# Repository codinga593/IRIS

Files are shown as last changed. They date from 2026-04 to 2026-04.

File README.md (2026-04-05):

# IRIS
IRIS Is a high powered model rocket focused on a precise propulsive landing on a custom tower, similar to SpaceX's falcon 9. It will fly on a H45 motor to approximately 700m, guiding itself to a waypoint in the air using aerodynamic fin control. It will then begin a controlled descent where fins attempt to maintain x and y pos. A landing motor (F15) then ignites to kill velocity, as thrust vectoring helps guide it to the tower where it will be caught by two motorised arms.

This project, while ambitous will be split into serveral mid power and high power flights to test subsystems and more. At the heart of the rocket is the amethyst flight computer, along with two extra boards- a compute module 5 and a raspberry pi zero 2 w. The compute module five will run non linear model predicitive control, an insanely powerful control algorithm to determine required X and Y accels to reach the target given fin or tvc limits. The STM32 based flight computer then turns these accelerations into concrete actuator commands. AN ADDED layer of abstraction is present for the fins in the form of field oriented control, which maintains torque to prevent backdriving.

Screenshot 2026-04-05 at 4 58 04 pm

Pictured above: FULL CAD of IRIS with transparent airframe for visibility

Screenshot 2026-03-22 at 3 32 23 pm

Pictured above: AMETHYST rocket flight computer. Note: Silkscreen colour is subject to change.

Screenshot 2026-03-17 at 5 57 23 pm

Pictured Above: Final Avionics Bay design on IRIS

# Bill of Materials (BOM)

| Designator | Part Name | Qty | Value / Part Number | Link |
|---|---:|---:|---|---|
| C66,C95,C26,C49,C28,C67,C55,C29,C33,C22,C48,C54,C19,C34,C30,C58,C41,C42,C20,C45,C46,C39,C18,C93,C47,C32,C21,C25,C27,C88,C35 | Ceramic Capacitor | 31 | 100nF, 0402, Samsung CL05B104KO5NNNC (JLC C1525) | [Link](https://jlcpcb.com/partdetail/1877-CL05B104KO5NNNC/C1525) |
| C23,C24,C61,C60 | Ceramic Capacitor | 4 | 24pF, 0402, C0G/NP0, FH 0402CG240J500NT (LCSC C1553) | [Link](https://www.lcsc.com/product-detail/C1553.html) |
| U3 | IMU | 1 | BNO085 (JLC C5189642) | [Link](https://jlcpcb.com/partdetail/CEVA-BNO085/C5189642) |
| J9,J1,J10,J11 | Socket Header | 4 | 1x03, 2.54mm, vertical, Amphenol SIP050-1X03-157BLF | [Link](https://www.digikey.com/en/products/detail/amphenol-cs-fci/SIP050-1X03-157BLF/1541044) |
| R45,R48,R46,R47,R49,R44 | Resistor | 6 | TBD - source BOM only says 'R' (exact value not specified) |  |
| R21,R14,R22,R17 | Resistor | 4 | 4.7kΩ, 0603, UNI-ROYAL 0603WAF4701T5E (LCSC C23162) | [Link](https://www.lcsc.com/product-detail/C23162.html) |
| TP13,TP9,TP14,TP6,TP11,TP10,TP16,TP15,TP5,TP8,TP7 | Test Point | 11 | PCB test pad 1.0x1.0mm - no discrete purchasable part specified |  |
| URpiZero1,UCM4 | Socket Header | 2 | 2x20 Raspberry Pi socket/riser header, Adafruit 4079 | [Link](https://www.digikey.com.au/en/products/detail/adafruit-industries-llc/4079/9858462) |
| R10,R18,R28 | Resistor | 3 | 100kΩ, 0402, UNI-ROYAL 0402WGF1003TCE (JLC/LCSC C25741) | [Link](https://www.lcsc.com/product-detail/C25741.html) |
| Q2,Q4,Q3 | MOSFET | 3 | BSZ100N06LS3 G, Infineon | [Link](https://www.digikey.com/en/products/detail/infineon-technologies/BSZ100N06LS3GATMA1/1936392) |
| C53,C92,C90,C94 | Ceramic Capacitor | 4 | 10uF, 0402, Samsung CL05A106MQ5NUNC (JLC C15525) | [Link](https://jlcpcb.com/partdetail/16204-CL05A106MQ5NUNC/C15525) |
| R6,R32,R8,R1 | Resistor | 4 | 100Ω, 0402, Ever Ohms CR0402F100RQ10 (JLC C429511) | [Link](https://jlcpcb.com/partdetail/Ever_OhmsTech-CR0402F100RQ10/C429511) |
| J14 | Pin Header | 1 | 1x04, 2.54mm, vertical, generic 4-pin header | [Link](https://newhavendisplay.com/1x4-single-row-pin-header-connector/) |
| J17 | RF Connector | 1 | Hirose U.FL-R-SMT(01) | [Link](https://www.digikey.com.au/en/products/detail/hirose-electric-co-ltd/U-FL-R-SMT-01/513010) |
| U5 | Barometer | 1 | MS5611-01BA03 / MS561101BA03-50 (JLC C15639) | [Link](https://jlcpcb.com/partdetail/TEConnectivity-MS561101BA0350/C15639) |
| C37 | Ceramic Capacitor | 1 | 10uF, 0603, Samsung CL10A106MA8NRNC (LCSC C96446) | [Link](https://www.lcsc.com/product-detail/C96446.html) |
| C91,C86,C89 | Ceramic Capacitor | 3 | 22uF, 0402, JLCPCB Assembly 22uF/16V (JLC C9900105298) | [Link](https://jlcpcb.com/partdetail/JLCPCBAssembly-22uF16V/C9900105298) |
| C84,C85 | Ceramic Capacitor | 2 | 10pF, 0402, FH 0402CG100J500NT (JLC C1545) | [Link](https://jlcpcb.com/partdetail/1897-0402CG100J500NT/C1545) |
| L11,L10,L9 | Inductor | 3 | 6.8uH, Würth WE-XHMA 6060 | [Link](https://www.mouser.com/ProductDetail/Wurth-Elektronik/74437368068) |
| R34,R33 | Resistor | 2 | 22Ω, 0402, YAGEO RC0402FR-0722RL (LCSC C114765) | [Link](https://www.lcsc.com/product-detail/C114765.html) |
| J5,J3,J4 | Terminal Block | 3 | Same Sky / CUI TB002-500-02BE | [Link](https://www.digikey.com.au/en/products/detail/same-sky-formerly-cui-devices/TB002-500-02BE/10064069) |
| Y1,Y3 | Crystal | 2 | 24MHz, 3225, Suzhou Liming 3225-24.00-20-10-10/A (JLC C518165) | [Link](https://jlcpcb.com/partdetail/534702-3225_24_00_20_10_10A/C518165) |
| C31 | Ceramic Capacitor | 1 | 10uF, 0402, Samsung CL05A106MQ5NUNC (JLC C15525) | [Link](https://jlcpcb.com/partdetail/16204-CL05A106MQ5NUNC/C15525) |
| J6 | JST Header | 1 | JST B5B-XH-A, 5-pin, 2.50mm, vertical | [Link](https://www.digikey.com/en/products/detail/jst-sales-america-inc/B5B-XH-A/1530483) |
| IC2 | LoRa Module | 1 | Seeed 114993390 / Wio-SX1262 | [Link](https://www.digikey.com/en/products/detail/seeed-technology-co-ltd/114993390/25835823) |
| U2 | LDO Regulator | 1 | AMS1117-3.3, SOT-223 (JLC C6186) | [Link](https://jlcpcb.com/partdetail/Advanced_MonolithicSystems-AMS1117_33/C6186) |
| U4 | IMU | 1 | ICM-42688-P (JLC C1850418) | [Link](https://jlcpcb.com/partdetail/TDKInvenSense-ICM_42688P/C1850418) |
| U11,U12,U13 | Buck Converter | 3 | TPS54525PWPR (JLC C140350) | [Link](https://jlcpcb.com/partdetail/TexasInstruments-TPS54525PWPR/C140350) |
| C36,C38,C56 | Ceramic Capacitor | 3 | 100nF, 0603, YAGEO CC0603KRX7R9BB104 (LCSC C14663) | [Link](https://www.lcsc.com/product-detail/C14663.html) |
| IC1 | NOR Flash | 1 | W25Q128JVFIQ (JLC C111478) | [Link](https://jlcpcb.com/partdetail/WinbondElec-W25Q128JVFIQ/C111478) |
| R15,R2,R7,R9,R11,R5,R29,R12,R27 | Resistor | 9 | 10kΩ, 0402, UNI-ROYAL 0402WGF1002TCE (JLC C25744) | [Link](https://jlcpcb.com/partdetail/26487-0402WGF1002TCE/C25744) |
| R3,R4 | Resistor | 2 | 1.5kΩ, 0402, UNI-ROYAL 0402WGF1501TCE (LCSC C25867) | [Link](https://www.lcsc.com/product-detail/C25867.html) |
| U1 | MCU | 1 | STM32H753ZIT6 (JLC C730207) | [Link](https://jlcpcb.com/partdetail/STMicroelectronics-STM32H753ZIT6/C730207) |
| C3,C2 | Ceramic Capacitor | 2 | 22uF, 0805, Samsung CL21A226MAYNNNE (LCSC C45783) | [Link](https://www.lcsc.com/product-detail/C45783.html) |
| C59 | Ceramic Capacitor | 1 | 10nF, 0402, Kyocera AVX 0402YC103K4T2A (JLC C2172121) | [Link](https://jlcpcb.com/partdetail/KyoceraAVX-0402YC103K4T2A/C2172121) |
| Y4 | Crystal | 1 | TBD - source BOM says only 'Crystal' in 2012 package |  |
| IC7 | Radar Sensor | 1 | Acconeer A121-001-T&R / A121 | [Link](https://www.mouser.com/ProductDetail/Acconeer/A121-001-TR) |
| D2 | LED | 1 | TBD - source BOM says only 'LED' in 0402 package |  |
| C1 | Ceramic Capacitor | 1 | 10uF, 0402, Samsung CL05A106MQ5NUNC (JLC C15525) | [Link](https://jlcpcb.com/partdetail/16204-CL05A106MQ5NUNC/C15525) |
| J7 | Molex PicoBlade Header | 1 | Molex 53261-0471 | [Link](https://www.digikey.com/en/products/detail/molex/0532610471/699096) |
| C40,C17 | Ceramic Capacitor | 2 | 2.2uF, 0402, Samsung CL05A225MQ5NSNC (JLC C12530) | [Link](https://jlcpcb.com/partdetail/13164-CL05A225MQ5NSNC/C12530) |
| J18 | USB Connector | 1 | Würth 629105150521, Micro USB B | [Link](https://www.digikey.com.au/en/products/detail/w%C3%BCrth-elektronik/629105150521/5047751) |
| U7 | Level Shifter | 1 | TXS0108EPWR (JLC C17206) | [Link](https://jlcpcb.com/partdetail/TexasInstruments-TXS0108EPWR/C17206) |
| FB1 | Ferrite Bead | 1 | Sunlord GZ1608D601TF (JLC C1002) | [Link](https://jlcpcb.com/partdetail/Sunlord-GZ1608D601TF/C1002) |
| D3 | Schottky Diode | 1 | BAT54A, SOT-23 (JLC C397609) | [Link](https://jlcpcb.com/partdetail/AnBon-BAT54A/C397609) |
| J12 | JST Header | 1 | JST S2B-XH-A, 2-pin, 2.50mm, right-angle | [Link](https://www.digikey.com/en/products/detail/jst-sales-america-inc/S2B-XH-A/1651055) |
| U10 | GNSS Module | 1 | u-blox MAX-M10S-00B (JLC C4153167) | [Link](https://jlcpcb.com/partdetail/UBLOX-MAX_M10S00B/C4153167) |
| J8 | XT30 Connector | 1 | AMASS XT30U-M (JLC C99101) | [Link](https://jlcpcb.com/partdetail/Changzhou_AmassElec-XT30UM/C99101) |
| R20,R19 | Resistor | 2 | 10kΩ, 0603, YAGEO RC0603FR-0710KL (LCSC C98220) | [Link](https://www.lcsc.com/product-detail/C98220.html) |
| J2 | JST Header | 1 | JST B2B-XH-A, 2-pin, 2.50mm, vertical | [Link](https://www.digikey.com/en/products/detail/jst-sales-america-inc/B2B-XH-A/1651045) |

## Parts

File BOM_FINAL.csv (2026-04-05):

Designator | Part Name | Qty | Value / Part Number | Link
C66,C95,C26,C49,C28,C67,C55,C29,C33,C22,C48,C54,C19,C34,C30,C58,C41,C42,C20,C45,C46,C39,C18,C93,C47,C32,C21,C25,C27,C88,C35 | Ceramic Capacitor | 31 | 100nF, 0402, Samsung CL05B104KO5NNNC (JLC C1525) | https://jlcpcb.com/partdetail/1877-CL05B104KO5NNNC/C1525
C23,C24,C61,C60 | Ceramic Capacitor | 4 | 24pF, 0402, C0G/NP0, FH 0402CG240J500NT (LCSC C1553) | https://www.lcsc.com/product-detail/C1553.html
U3 | IMU | 1 | BNO085 (JLC C5189642) | https://jlcpcb.com/partdetail/CEVA-BNO085/C5189642
J9,J1,J10,J11 | Socket Header | 4 | 1x03, 2.54mm, vertical, Amphenol SIP050-1X03-157BLF | https://www.digikey.com/en/products/detail/amphenol-cs-fci/SIP050-1X03-157BLF/1541044
R45,R48,R46,R47,R49,R44 | Resistor | 6 | TBD - source BOM only says 'R' (exact value not specified)
R21,R14,R22,R17 | Resistor | 4 | 4.7kΩ, 0603, UNI-ROYAL 0603WAF4701T5E (LCSC C23162) | https://www.lcsc.com/product-detail/C23162.html
TP13,TP9,TP14,TP6,TP11,TP10,TP16,TP15,TP5,TP8,TP7 | Test Point | 11 | PCB test pad 1.0x1.0mm - no discrete purchasable part specified
URpiZero1,UCM4 | Socket Header | 2 | 2x20 Raspberry Pi socket/riser header, Adafruit 4079 | https://www.digikey.com.au/en/products/detail/adafruit-industries-llc/4079/9858462
R10,R18,R28 | Resistor | 3 | 100kΩ, 0402, UNI-ROYAL 0402WGF1003TCE (JLC/LCSC C25741) | https://www.lcsc.com/product-detail/C25741.html
Q2,Q4,Q3 | MOSFET | 3 | BSZ100N06LS3 G, Infineon | https://www.digikey.com/en/products/detail/infineon-technologies/BSZ100N06LS3GATMA1/1936392
C53,C92,C90,C94 | Ceramic Capacitor | 4 | 10uF, 0402, Samsung CL05A106MQ5NUNC (JLC C15525) | https://jlcpcb.com/partdetail/16204-CL05A106MQ5NUNC/C15525
R6,R32,R8,R1 | Resistor | 4 | 100Ω, 0402, Ever Ohms CR0402F100RQ10 (JLC C429511) | https://jlcpcb.com/partdetail/Ever_OhmsTech-CR0402F100RQ10/C429511
J14 | Pin Header | 1 | 1x04, 2.54mm, vertical, generic 4-pin header | https://newhavendisplay.com/1x4-single-row-pin-header-connector/
J17 | RF Connector | 1 | Hirose U.FL-R-SMT(01) | https://www.digikey.com.au/en/products/detail/hirose-electric-co-ltd/U-FL-R-SMT-01/513010
U5 | Barometer | 1 | MS5611-01BA03 / MS561101BA03-50 (JLC C15639) | https://jlcpcb.com/partdetail/TEConnectivity-MS561101BA0350/C15639
C37 | Ceramic Capacitor | 1 | 10uF, 0603, Samsung CL10A106MA8NRNC (LCSC C96446) | https://www.lcsc.com/product-detail/C96446.html
C91,C86,C89 | Ceramic Capacitor | 3 | 22uF, 0402, JLCPCB Assembly 22uF/16V (JLC C9900105298) | https://jlcpcb.com/partdetail/JLCPCBAssembly-22uF16V/C9900105298
C84,C85 | Ceramic Capacitor | 2 | 10pF, 0402, FH 0402CG100J500NT (JLC C1545) | https://jlcpcb.com/partdetail/1897-0402CG100J500NT/C1545
L11,L10,L9 | Inductor | 3 | 6.8uH, Würth WE-XHMA 6060 | https://www.mouser.com/ProductDetail/Wurth-Elektronik/74437368068
R34,R33 | Resistor | 2 | 22Ω, 0402, YAGEO RC0402FR-0722RL (LCSC C114765) | https://www.lcsc.com/product-detail/C114765.html
J5,J3,J4 | Terminal Block | 3 | Same Sky / CUI TB002-500-02BE | https://www.digikey.com.au/en/products/detail/same-sky-formerly-cui-devices/TB002-500-02BE/10064069
Y1,Y3 | Crystal | 2 | 24MHz, 3225, Suzhou Liming 3225-24.00-20-10-10/A (JLC C518165) | https://jlcpcb.com/partdetail/534702-3225_24_00_20_10_10A/C518165
C31 | Ceramic Capacitor | 1 | 10uF, 0402, Samsung CL05A106MQ5NUNC (JLC C15525) | https://jlcpcb.com/partdetail/16204-CL05A106MQ5NUNC/C15525
J6 | JST Header | 1 | JST B5B-XH-A, 5-pin, 2.50mm, vertical | https://www.digikey.com/en/products/detail/jst-sales-america-inc/B5B-XH-A/1530483
IC2 | LoRa Module | 1 | Seeed 114993390 / Wio-SX1262 | https://www.digikey.com/en/products/detail/seeed-technology-co-ltd/114993390/25835823
U2 | LDO Regulator | 1 | AMS1117-3.3, SOT-223 (JLC C6186) | https://jlcpcb.com/partdetail/Advanced_MonolithicSystems-AMS1117_33/C6186
U4 | IMU | 1 | ICM-42688-P (JLC C1850418) | https://jlcpcb.com/partdetail/TDKInvenSense-ICM_42688P/C1850418
U11,U12,U13 | Buck Converter | 3 | TPS54525PWPR (JLC C140350) | https://jlcpcb.com/partdetail/TexasInstruments-TPS54525PWPR/C140350
C36,C38,C56 | Ceramic Capacitor | 3 | 100nF, 0603, YAGEO CC0603KRX7R9BB104 (LCSC C14663) | https://www.lcsc.com/product-detail/C14663.html
IC1 | NOR Flash | 1 | W25Q128JVFIQ (JLC C111478) | https://jlcpcb.com/partdetail/WinbondElec-W25Q128JVFIQ/C111478
R15,R2,R7,R9,R11,R5,R29,R12,R27 | Resistor | 9 | 10kΩ, 0402, UNI-ROYAL 0402WGF1002TCE (JLC C25744) | https://jlcpcb.com/partdetail/26487-0402WGF1002TCE/C25744
R3,R4 | Resistor | 2 | 1.5kΩ, 0402, UNI-ROYAL 0402WGF1501TCE (LCSC C25867) | https://www.lcsc.com/product-detail/C25867.html
U1 | MCU | 1 | STM32H753ZIT6 (JLC C730207) | https://jlcpcb.com/partdetail/STMicroelectronics-STM32H753ZIT6/C730207
C3,C2 | Ceramic Capacitor | 2 | 22uF, 0805, Samsung CL21A226MAYNNNE (LCSC C45783) | https://www.lcsc.com/product-detail/C45783.html
C59 | Ceramic Capacitor | 1 | 10nF, 0402, Kyocera AVX 0402YC103K4T2A (JLC C2172121) | https://jlcpcb.com/partdetail/KyoceraAVX-0402YC103K4T2A/C2172121
Y4 | Crystal | 1 | TBD - source BOM says only 'Crystal' in 2012 package
IC7 | Radar Sensor | 1 | Acconeer A121-001-T&R / A121 | https://www.mouser.com/ProductDetail/Acconeer/A121-001-TR
D2 | LED | 1 | TBD - source BOM says only 'LED' in 0402 package
C1 | Ceramic Capacitor | 1 | 10uF, 0402, Samsung CL05A106MQ5NUNC (JLC C15525) | https://jlcpcb.com/partdetail/16204-CL05A106MQ5NUNC/C15525
J7 | Molex PicoBlade Header | 1 | Molex 53261-0471 | https://www.digikey.com/en/products/detail/molex/0532610471/699096
C40,C17 | Ceramic Capacitor | 2 | 2.2uF, 0402, Samsung CL05A225MQ5NSNC (JLC C12530) | https://jlcpcb.com/partdetail/13164-CL05A225MQ5NSNC/C12530
J18 | USB Connector | 1 | Würth 629105150521, Micro USB B | https://www.digikey.com.au/en/products/detail/w%C3%BCrth-elektronik/629105150521/5047751
U7 | Level Shifter | 1 | TXS0108EPWR (JLC C17206) | https://jlcpcb.com/partdetail/TexasInstruments-TXS0108EPWR/C17206
FB1 | Ferrite Bead | 1 | Sunlord GZ1608D601TF (JLC C1002) | https://jlcpcb.com/partdetail/Sunlord-GZ1608D601TF/C1002
D3 | Schottky Diode | 1 | BAT54A, SOT-23 (JLC C397609) | https://jlcpcb.com/partdetail/AnBon-BAT54A/C397609
J12 | JST Header | 1 | JST S2B-XH-A, 2-pin, 2.50mm, right-angle | https://www.digikey.com/en/products/detail/jst-sales-america-inc/S2B-XH-A/1651055
U10 | GNSS Module | 1 | u-blox MAX-M10S-00B (JLC C4153167) | https://jlcpcb.com/partdetail/UBLOX-MAX_M10S00B/C4153167
J8 | XT30 Connector | 1 | AMASS XT30U-M (JLC C99101) | https://jlcpcb.com/partdetail/Changzhou_AmassElec-XT30UM/C99101
R20,R19 | Resistor | 2 | 10kΩ, 0603, YAGEO RC0603FR-0710KL (LCSC C98220) | https://www.lcsc.com/product-detail/C98220.html
J2 | JST Header | 1 | JST B2B-XH-A, 2-pin, 2.50mm, vertical | https://www.digikey.com/en/products/detail/jst-sales-america-inc/B2B-XH-A/1651045

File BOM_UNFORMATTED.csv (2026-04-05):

Id | Designator | Footprint | Quantity | Designation | Supplier and ref
1 | C66,C95,C26,C49,C28,C67,C55,C29,C33,C22,C48,C54,C19,C34,C30,C58,C41,C42,C20,C45,C46,C39,C18,C93,C47,C32,C21,C25,C27,C88,C35 | C_0402_1005Metric | 31 | 100n
2 | C23,C24,C61,C60 | C_0402_1005Metric | 4 | 24pf
3 | U3 | IC_BNO085 | 1 | BNO085
4 | J9,J1,J10,J11 | PinHeader_1x03_P2.54mm_Vertical | 4 | Conn_01x03_Socket
5 | R45,R48,R46,R47,R49,R44 | R_0402_1005Metric | 6 | R
6 | R21,R14,R22,R17 | R_0603_1608Metric | 4 | 4.7k
7 | TP13,TP9,TP14,TP6,TP11,TP10,TP16,TP15,TP5,TP8,TP12 | TestPoint_Pad_1.0x1.0mm | 11 | TestPoint
8 | URpiZero1,UCM4 | PinSocket_2x20_P2.54mm_Vertical_SMD | 2 | ~
9 | R10,R18,R28 | R_0402_1005Metric | 3 | 100k
10 | Q2,Q4,Q3 | TRANS_BSZ100N06LS3_G | 3 | BSZ100N06LS3_G
11 | C53,C92,C90,C94 | C_0402_1005Metric | 4 | 10u
12 | R6,R32,R8,R1 | R_0402_1005Metric | 4 | 100Ω
13 | J14 | PinHeader_1x04_P2.54mm_Vertical | 1 | Conn_01x04
14 | J17 | HRS_U.FL-R-SMT_01_ | 1 | U.FL-R-SMT_01_
15 | U5 | LGA-8_3x5mm_P1.25mm | 1 | MS5611-01BA
16 | C37 | C_0603_1608Metric | 1 | 10u
17 | C91,C86,C89 | C_0402_1005Metric | 3 | 22u
18 | C84,C85 | C_0402_1005Metric | 2 | 10pf
19 | L11,L10,L9 | WE-XHMA_6060 | 3 | 6.8 µH
20 | R34,R33 | R_0402_1005Metric | 2 | 22
21 | J5,J3,J4 | CUI_TB002-500-02BE | 3 | Conn_01x02
22 | Y1,Y3 | TSX-3225 | 2 | 24mhz
23 | C31 | C_0402_1005Metric | 1 | 10uf
24 | J6 | JST_XH_B5B-XH-A_1x05_P2.50mm_Vertical | 1 | Conn_01x05_Pin
25 | IC2 | 114993390 | 1 | 114993390
26 | U2 | SOT-223-3_TabPin2 | 1 | AMS1117-3.3
27 | U4 | PQFN50P300X250X97-14N | 1 | ICM-42688-P
28 | U11,U12,U13 | PWP14_2P31X2P46_TEX | 3 | TPS54525PWPR
29 | C36,C38,C56 | C_0603_1608Metric | 3 | 100n
30 | IC1 | SOIC127P1032X264-16N | 1 | W25Q128JVFIQ
31 | R15,R2,R7,R9,R11,R5,R29,R12,R27 | R_0402_1005Metric | 9 | 10k
32 | R3,R4 | R_0402_1005Metric | 2 | 1k5
33 | U1 | QFP50P2200X2200X160-144N | 1 | STM32H753ZIT6
34 | C3,C2 | C_0805_2012Metric | 2 | 22u
35 | C59 | C_0402_1005Metric | 1 | 10n
36 | Y4 | Crystal_SMD_2012-2Pin_2.0x1.2mm | 1 | Crystal
37 | IC7 | A121001TR | 1 | A121-001-T&R
38 | D2 | LED_0402_1005Metric | 1 | LED
39 | C1 | C_0402_1005Metric | 1 | 10uF
40 | J7 | MOLEX_532610471 | 1 | 532610471
41 | C40,C17 | C_0402_1005Metric | 2 | 2.2u
42 | J18 | USB_Micro-B_Wuerth_629105150521 | 1 | USB_B_Micro
43 | U7 | TSSOP-20_4.4x6.5mm_P0.65mm | 1 | TXS0108EPW
44 | FB1 | IND_GZ1608_SNL | 1 | 120R
45 | D3 | SOT-23 | 1 | BAT54A
46 | J12 | JST_XH_S2B-XH-A_1x02_P2.50mm_Horizontal | 1 | Conn_01x02
47 | U10 | XCVR_MAX-M10S-00B | 1 | MAX-M10S-00B
48 | J8 | AMASS_XT30U-M_1x02_P5.0mm_Vertical | 1 | Conn_01x02_Pin
49 | R20,R19 | R_0603_1608Metric | 2 | 10k
50 | J2 | JST_XH_B2B-XH-A_1x02_P2.50mm_Vertical | 1 | Conn_01x02_Pin

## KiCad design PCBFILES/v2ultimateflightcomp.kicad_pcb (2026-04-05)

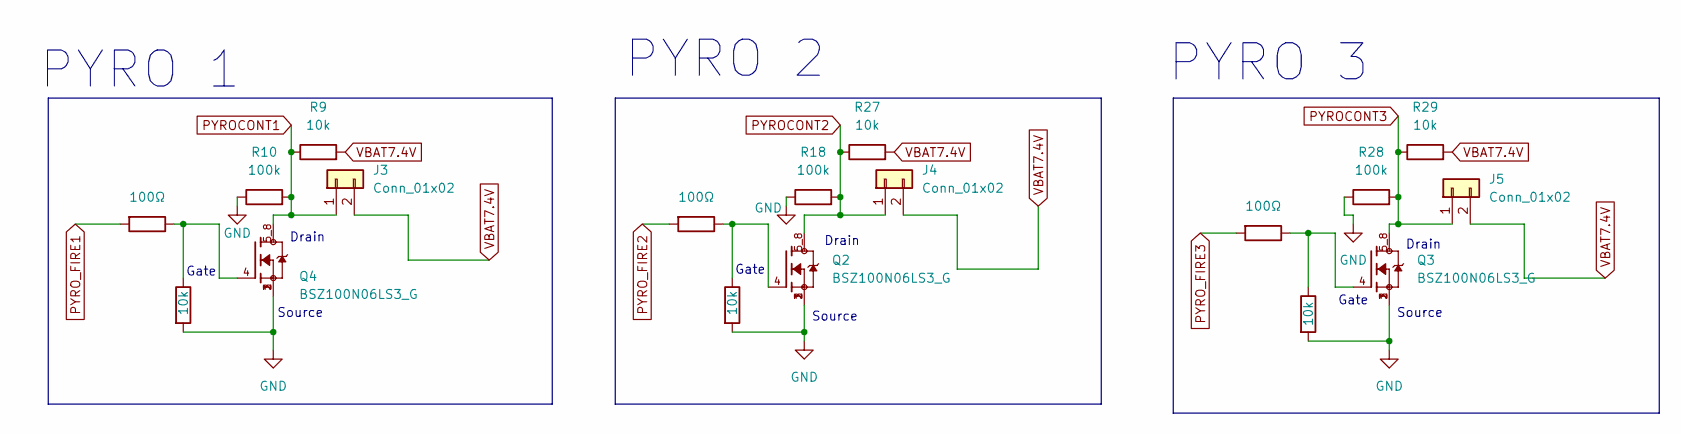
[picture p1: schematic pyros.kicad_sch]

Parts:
J3, J4, J5: Conn_01x02; CUI_TB002-500-02BE
Q2, Q3, Q4: BSZ100N06LS3_G; TRANS_BSZ100N06LS3_G; PARTREV 2.4
R1, R6, R8: 100Ω; R_0402_1005Metric
R2, R5, R7, R9, R27, R29: 10k; R_0402_1005Metric
R10, R18, R28: 100k; R_0402_1005Metric

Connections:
GND: Q2.1, Q2.2, Q2.3, Q3.1, Q3.2, Q3.3, Q4.1, Q4.2, Q4.3, R2.2, R5.2, R7.2, R10.1, R18.1, R28.1; also elsewhere on the board
unnamed: Q2.4, R5.1, R6.1
unnamed: Q3.4, R7.1, R8.1
unnamed: Q4.4, R1.1, R2.1
PYROCONT1: J3.1, Q4.5_8, R9.1, R10.2; also elsewhere on the board
PYROCONT2: J4.1, Q2.5_8, R18.2, R27.1; also elsewhere on the board
PYROCONT3: J5.1, Q3.5_8, R28.2, R29.1; also elsewhere on the board
PYRO_FIRE1: R1.2; also elsewhere on the board
PYRO_FIRE2: R6.2; also elsewhere on the board
PYRO_FIRE3: R8.2; also elsewhere on the board
VBAT7.4V: J3.2, J4.2, J5.2, R9.2, R27.2, R29.2; also elsewhere on the board

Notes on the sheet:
PYRO 3
Gate
PYRO 2
Source
Drain
PYRO 1

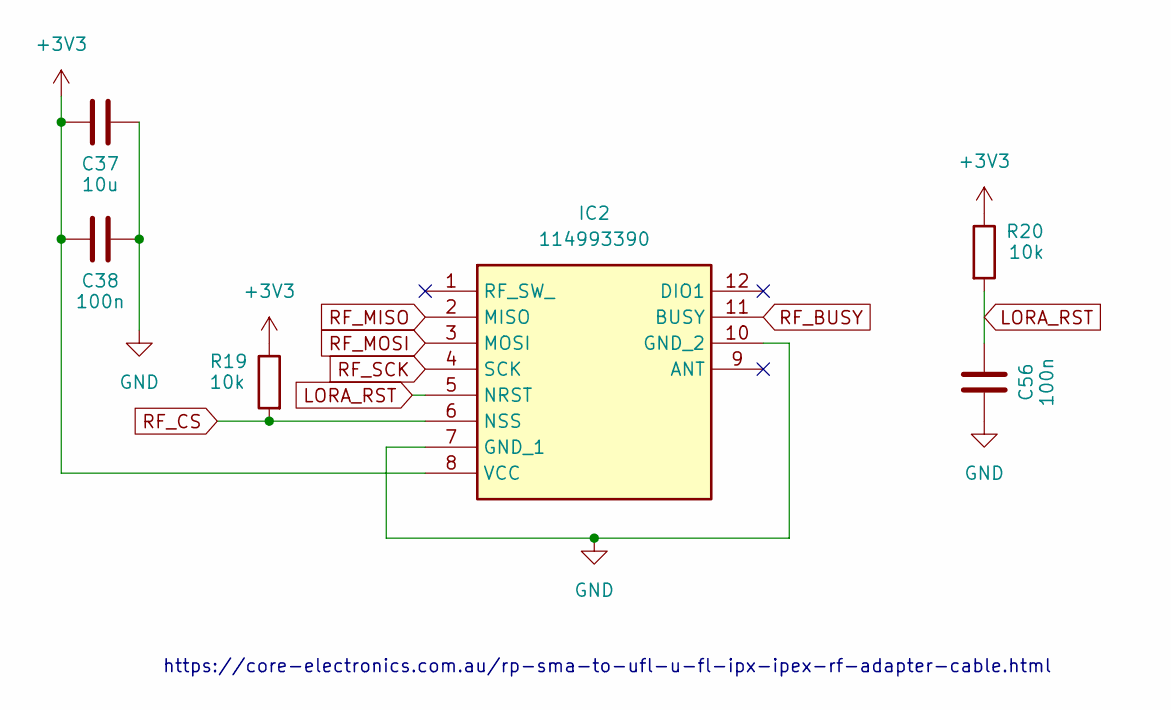
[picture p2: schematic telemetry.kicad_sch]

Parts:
C37: 10u; C_0603_1608Metric
C38, C56: 100n; C_0603_1608Metric
IC2: 114993390; Mouser Part Number 713-114993390
R19, R20: 10k; R_0603_1608Metric

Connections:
+3V3: C37.1, C38.1, IC2.8 (VCC), R19.1, R20.1; also elsewhere on the board
GND: C37.2, C38.2, C56.1, IC2.7 (GND_1), IC2.10 (GND_2); also elsewhere on the board
LORA_RST: C56.2, IC2.5 (NRST), R20.2; also elsewhere on the board
RF_BUSY: IC2.11 (BUSY); also elsewhere on the board
RF_CS: IC2.6 (NSS), R19.2; also elsewhere on the board
RF_MISO: IC2.2 (MISO); also elsewhere on the board
RF_MOSI: IC2.3 (MOSI); also elsewhere on the board
RF_SCK: IC2.4 (SCK); also elsewhere on the board

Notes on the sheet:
https://core-electronics.com.au/rp-sma-to-ufl-u-fl-ipx-ipex-rf-adapter-cable.html

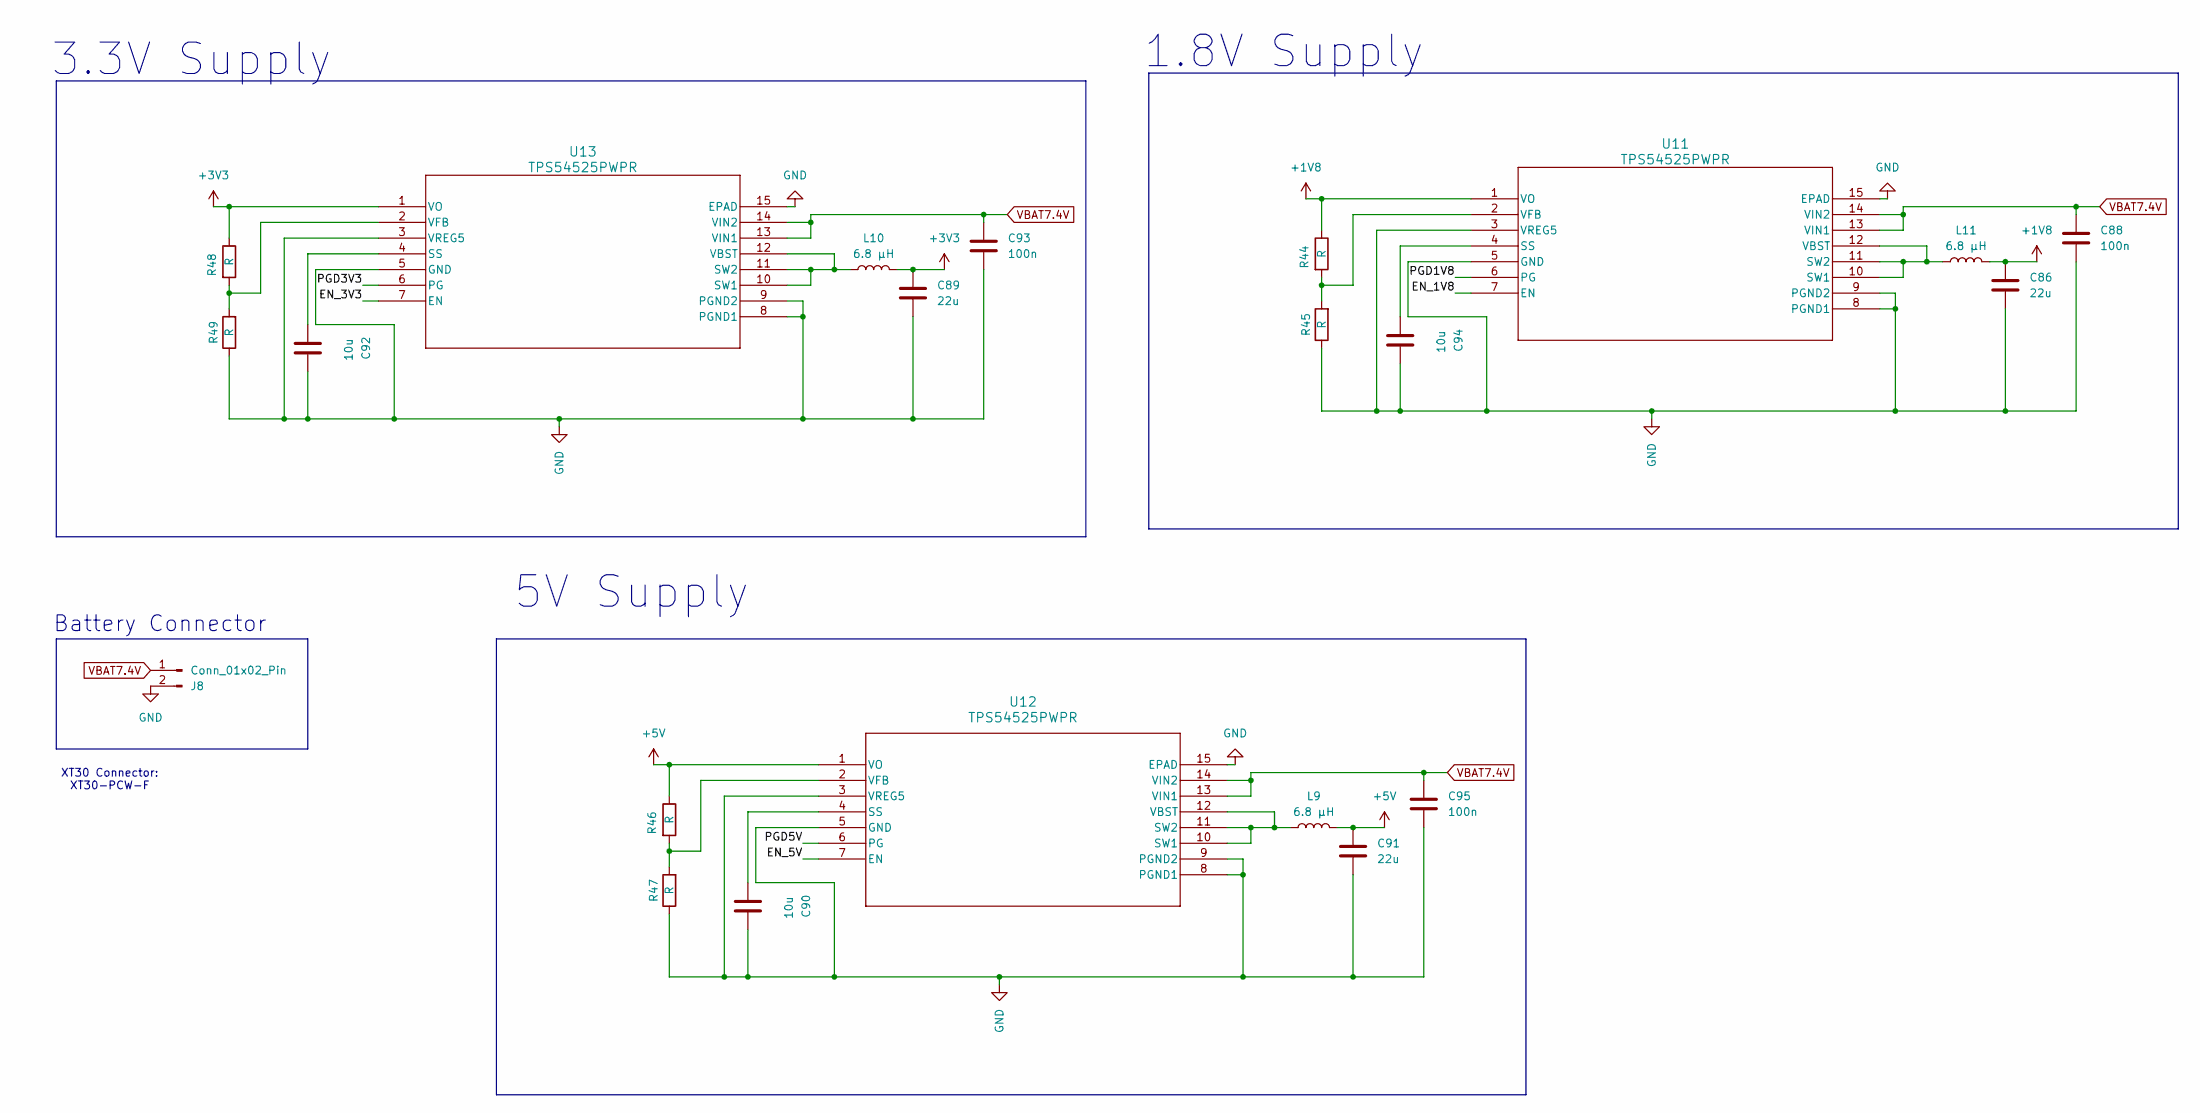
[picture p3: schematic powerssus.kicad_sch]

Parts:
C86, C89, C91: 22u; C_0402_1005Metric
C88, C93, C95: 100n; C_0402_1005Metric
C90, C92, C94: 10u; C_0402_1005Metric
J8: Conn_01x02_Pin; AMASS_XT30U-M_1x02_P5.0mm_Vertical
L9, L10, L11: 6.8 µH; WE-XHMA_6060
R44, R45, R46, R47, R48, R49: R; R_0402_1005Metric
U11, U12, U13: TPS54525PWPR; PWP14_2P31X2P46_TEX

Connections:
+1V8: C86.1, L11.2, R44.1, U11.1 (VO); also elsewhere on the board
+3V3: C89.1, L10.2, R48.1, U13.1 (VO); also elsewhere on the board
+5V: C91.1, L9.2, R46.1, U12.1 (VO); also elsewhere on the board
/Power/EN_1V8: U11.7 (EN)
/Power/EN_3V3: U13.7 (EN)
/Power/EN_5V: U12.7 (EN)
/Power/PGD1V8: U11.6 (PG)
/Power/PGD3V3: U13.6 (PG)
/Power/PGD5V: U12.6 (PG)
GND: C86.2, C88.2, C89.2, C90.1, C91.2, C92.1, C93.2, C94.1, C95.2, J8.2, R45.1, R47.1, R49.1, U11.3 (VREG5), U11.5 (GND), U11.8 (PGND1), U11.9 (PGND2), U11.15 (EPAD), U12.3 (VREG5), U12.5 (GND), U12.8 (PGND1), U12.9 (PGND2), U12.15 (EPAD), U13.3 (VREG5), U13.5 (GND), U13.8 (PGND1), U13.9 (PGND2), U13.15 (EPAD); also elsewhere on the board
unnamed: C94.2, U11.4 (SS)
unnamed: L11.1, U11.10 (SW1), U11.11 (SW2), U11.12 (VBST)
unnamed: R44.2, R45.2, U11.2 (VFB)
unnamed: C90.2, U12.4 (SS)
unnamed: L9.1, U12.10 (SW1), U12.11 (SW2), U12.12 (VBST)
unnamed: R46.2, R47.2, U12.2 (VFB)
unnamed: C92.2, U13.4 (SS)
unnamed: L10.1, U13.10 (SW1), U13.11 (SW2), U13.12 (VBST)
unnamed: R48.2, R49.2, U13.2 (VFB)
VBAT7.4V: C88.1, C93.1, C95.1, J8.1, U11.13 (VIN1), U11.14 (VIN2), U12.13 (VIN1), U12.14 (VIN2), U13.13 (VIN1), U13.14 (VIN2); also elsewhere on the board

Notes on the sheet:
5V Supply
1.8V Supply
XT30 Connector: XT30-PCW-F
3.3V Supply
Battery Connector

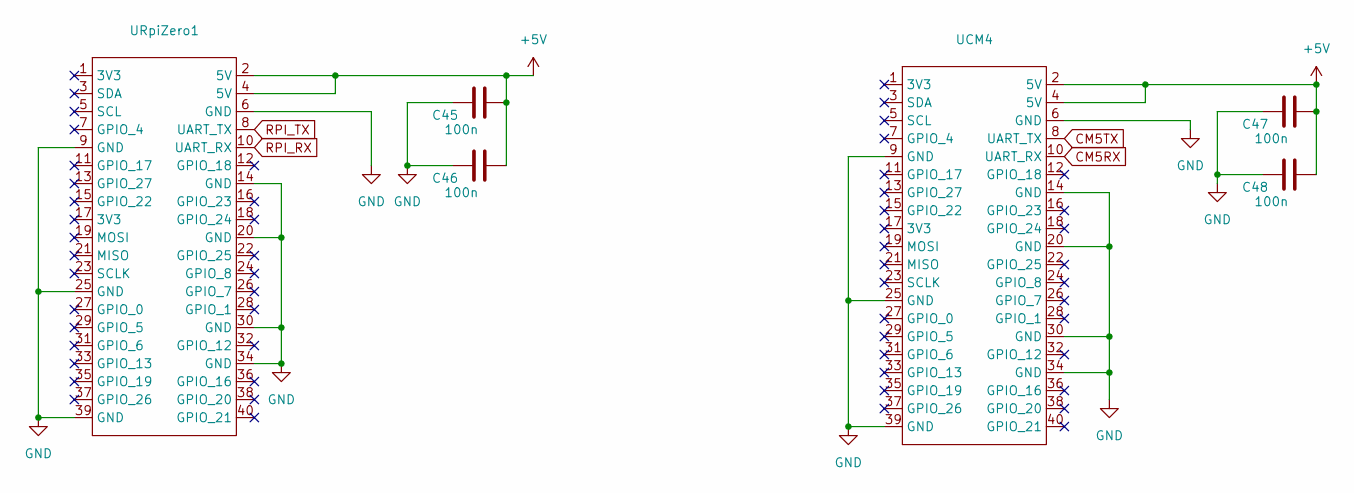
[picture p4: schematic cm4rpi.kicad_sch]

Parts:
C45, C46, C47, C48: 100n; C_0402_1005Metric
UCM4: PinSocket_2x20_P2.54mm_Vertical_SMD
URpiZero1: PinSocket_2x20_P2.54mm_Vertical_SMD

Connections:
+5V: C45.2, C46.2, C47.2, C48.2, UCM4.2 (5V), UCM4.4 (5V), URpiZero1.2 (5V), URpiZero1.4 (5V); also elsewhere on the board
CM5RX: UCM4.10 (UART_RX); also elsewhere on the board
CM5TX: UCM4.8 (UART_TX); also elsewhere on the board
GND: C45.1, C46.1, C47.1, C48.1, UCM4.6 (GND), UCM4.9 (GND), UCM4.14 (GND), UCM4.20 (GND), UCM4.25 (GND), UCM4.30 (GND), UCM4.34 (GND), UCM4.39 (GND), URpiZero1.6 (GND), URpiZero1.9 (GND), URpiZero1.14 (GND), URpiZero1.20 (GND), URpiZero1.25 (GND), URpiZero1.30 (GND), URpiZero1.34 (GND), URpiZero1.39 (GND); also elsewhere on the board
RPI_RX: URpiZero1.10 (UART_RX); also elsewhere on the board
RPI_TX: URpiZero1.8 (UART_TX); also elsewhere on the board

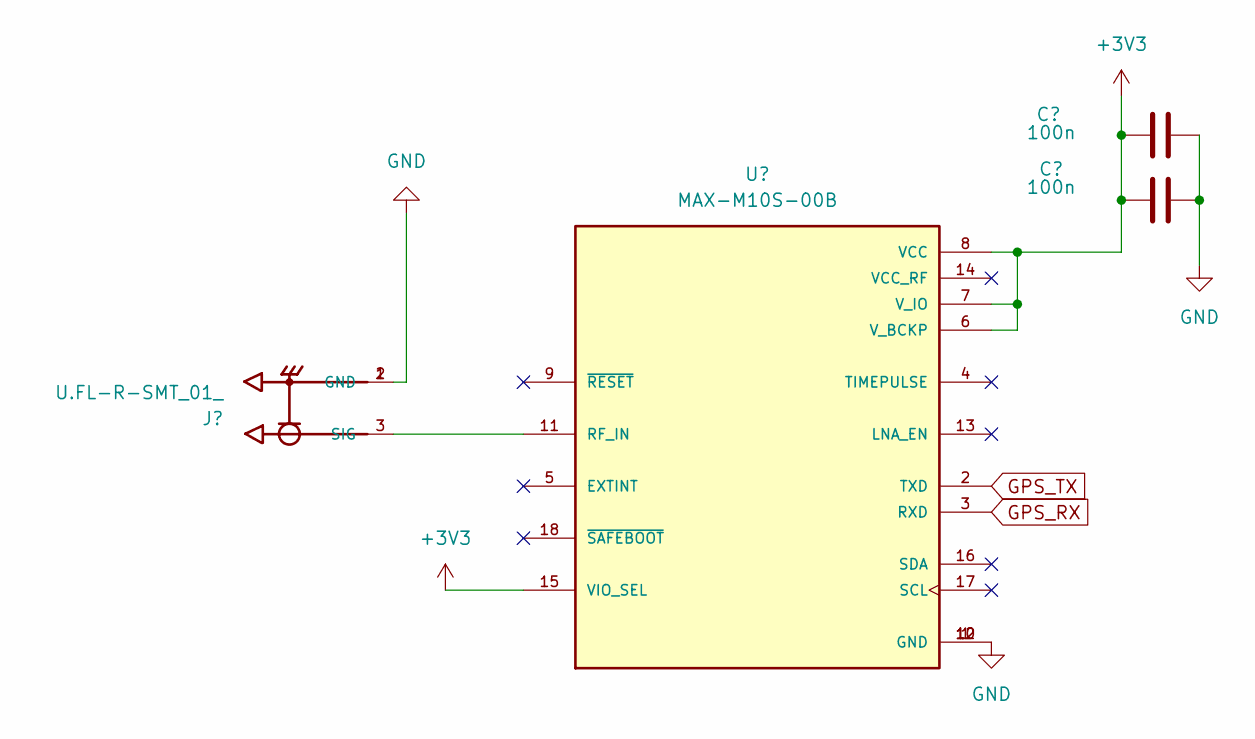
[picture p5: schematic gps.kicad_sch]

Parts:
C54, C55: 100n; C_0402_1005Metric
J17: U.FL-R-SMT_01_; HRS_U.FL-R-SMT_01_
U10: MAX-M10S-00B; XCVR_MAX-M10S-00B; PARTREV C1

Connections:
+3V3: C54.1, C55.1, U10.6 (V_BCKP), U10.7 (V_IO), U10.8 (VCC), U10.15 (VIO_SEL); also elsewhere on the board
GND: C54.2, C55.2, J17.1 (GND), J17.2 (GND), U10.1 (GND), U10.10 (GND), U10.12 (GND); also elsewhere on the board
GPS_RX: U10.3 (RXD); also elsewhere on the board
GPS_TX: U10.2 (TXD); also elsewhere on the board
unnamed: J17.3 (SIG), U10.11 (RF_IN)

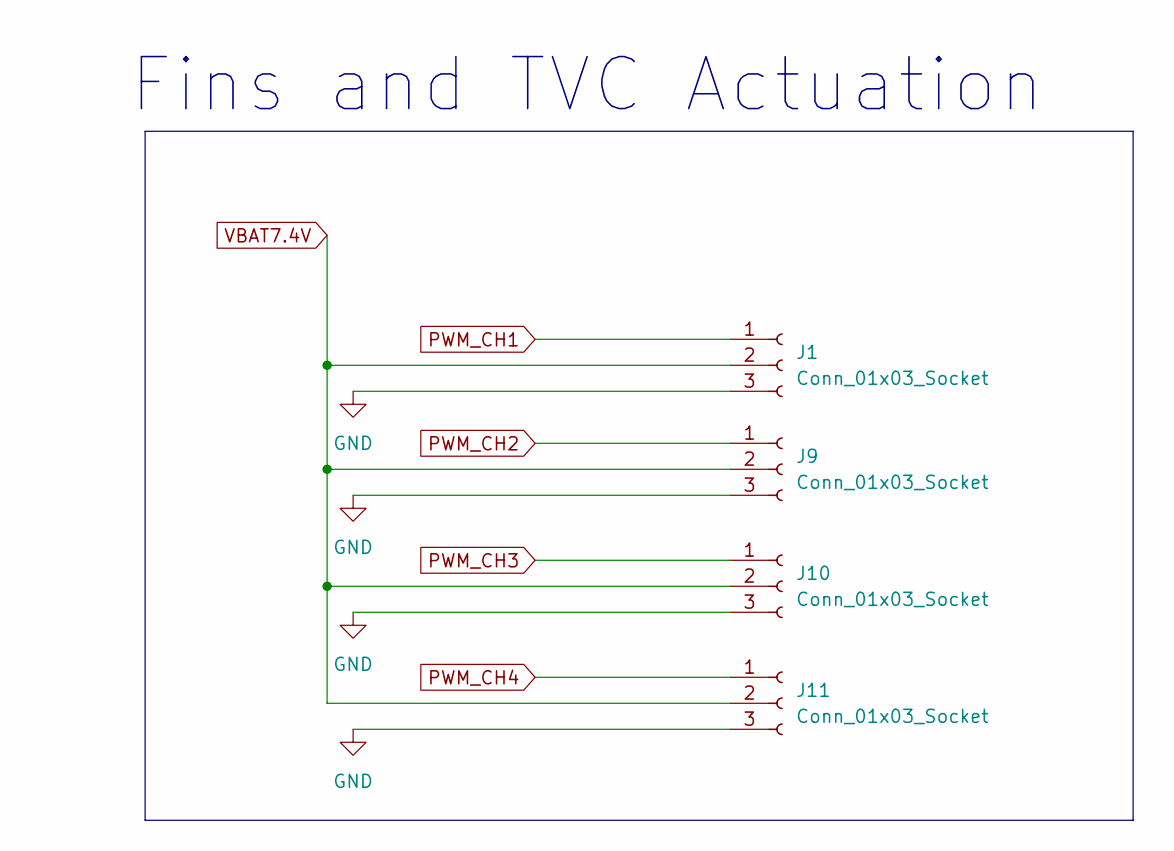
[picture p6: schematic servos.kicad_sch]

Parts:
J1, J9, J10, J11: Conn_01x03_Socket; PinHeader_1x03_P2.54mm_Vertical

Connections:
GND: J1.3, J9.3, J10.3, J11.3; also elsewhere on the board
PWM_CH1: J1.1; also elsewhere on the board
PWM_CH2: J9.1; also elsewhere on the board
PWM_CH3: J10.1; also elsewhere on the board
PWM_CH4: J11.1; also elsewhere on the board
VBAT7.4V: J1.2, J9.2, J10.2, J11.2; also elsewhere on the board

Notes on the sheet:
Fins and TVC Actuation

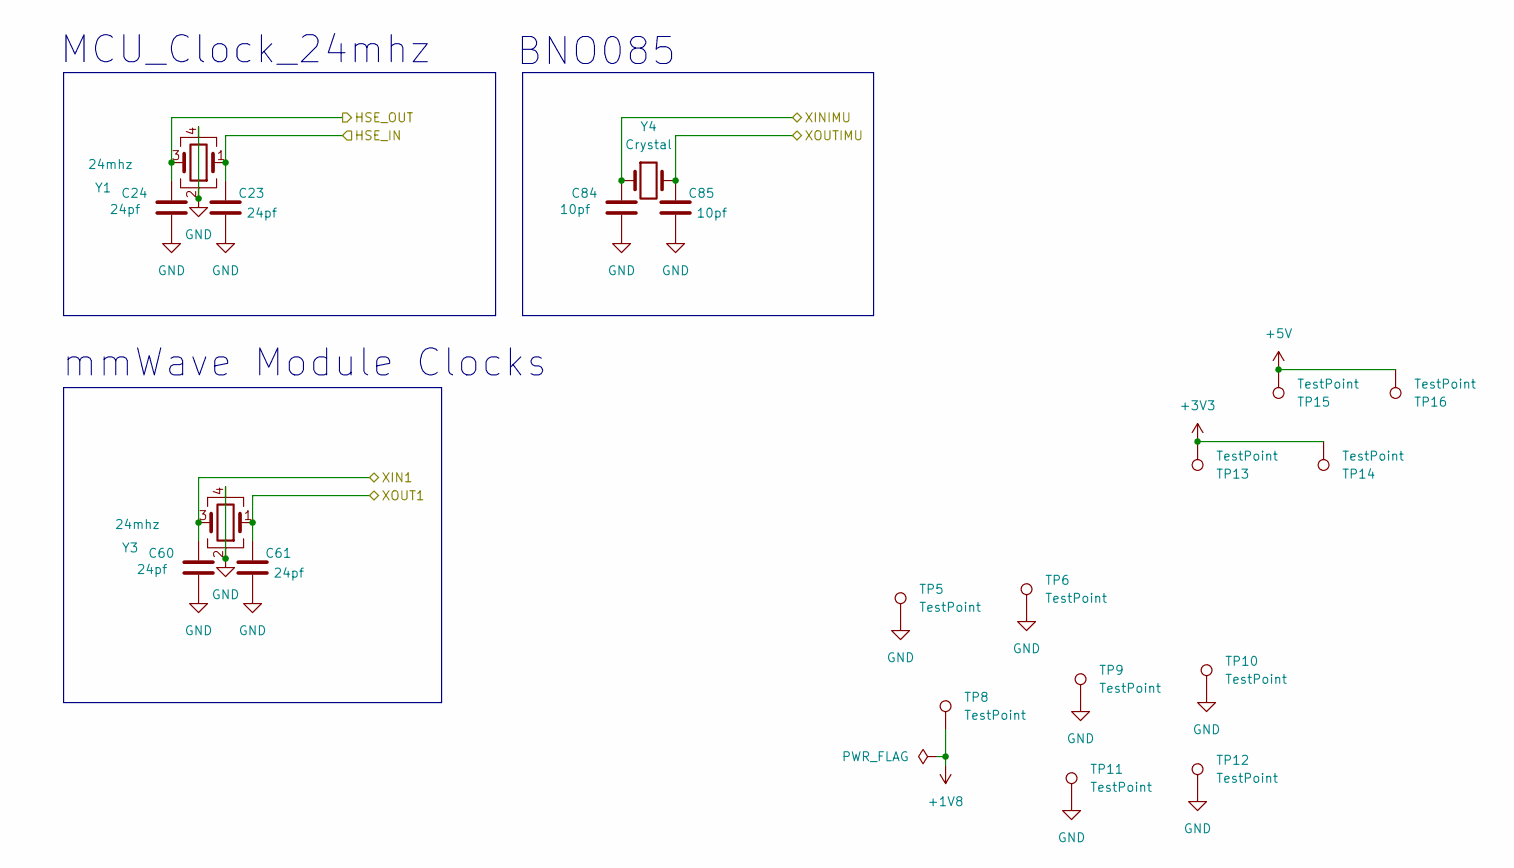
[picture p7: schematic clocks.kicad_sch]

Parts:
C23, C24, C60, C61: 24pf; C_0402_1005Metric
C84, C85: 10pf; C_0402_1005Metric
TP5, TP6, TP8, TP9, TP10, TP11, TP12, TP13, TP14, TP15, TP16: TestPoint; TestPoint_Pad_1.0x1.0mm
Y1, Y3: 24mhz; TSX-3225
Y4: Crystal; Crystal_SMD_2012-2Pin_2.0x1.2mm

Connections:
+1V8: TP8.1; also elsewhere on the board
+3V3: TP13.1, TP14.1; also elsewhere on the board
+5V: TP15.1, TP16.1; also elsewhere on the board
/Clocks/HSE_IN: C23.1, Y1.1; also elsewhere on the board
/Clocks/HSE_OUT: C24.1, Y1.3; also elsewhere on the board
/Clocks/XIN1: C60.1, Y3.3; also elsewhere on the board
/Clocks/XINIMU: C84.1, Y4.1; also elsewhere on the board
/Clocks/XOUT1: C61.1, Y3.1; also elsewhere on the board
/Clocks/XOUTIMU: C85.1, Y4.2; also elsewhere on the board
GND: C23.2, C24.2, C60.2, C61.2, C84.2, C85.2, TP5.1, TP6.1, TP9.1, TP10.1, TP11.1, TP12.1, Y1.2, Y1.4, Y3.2, Y3.4; also elsewhere on the board

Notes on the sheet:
mmWave Module Clocks
BNO085
MCU_Clock_24mhz

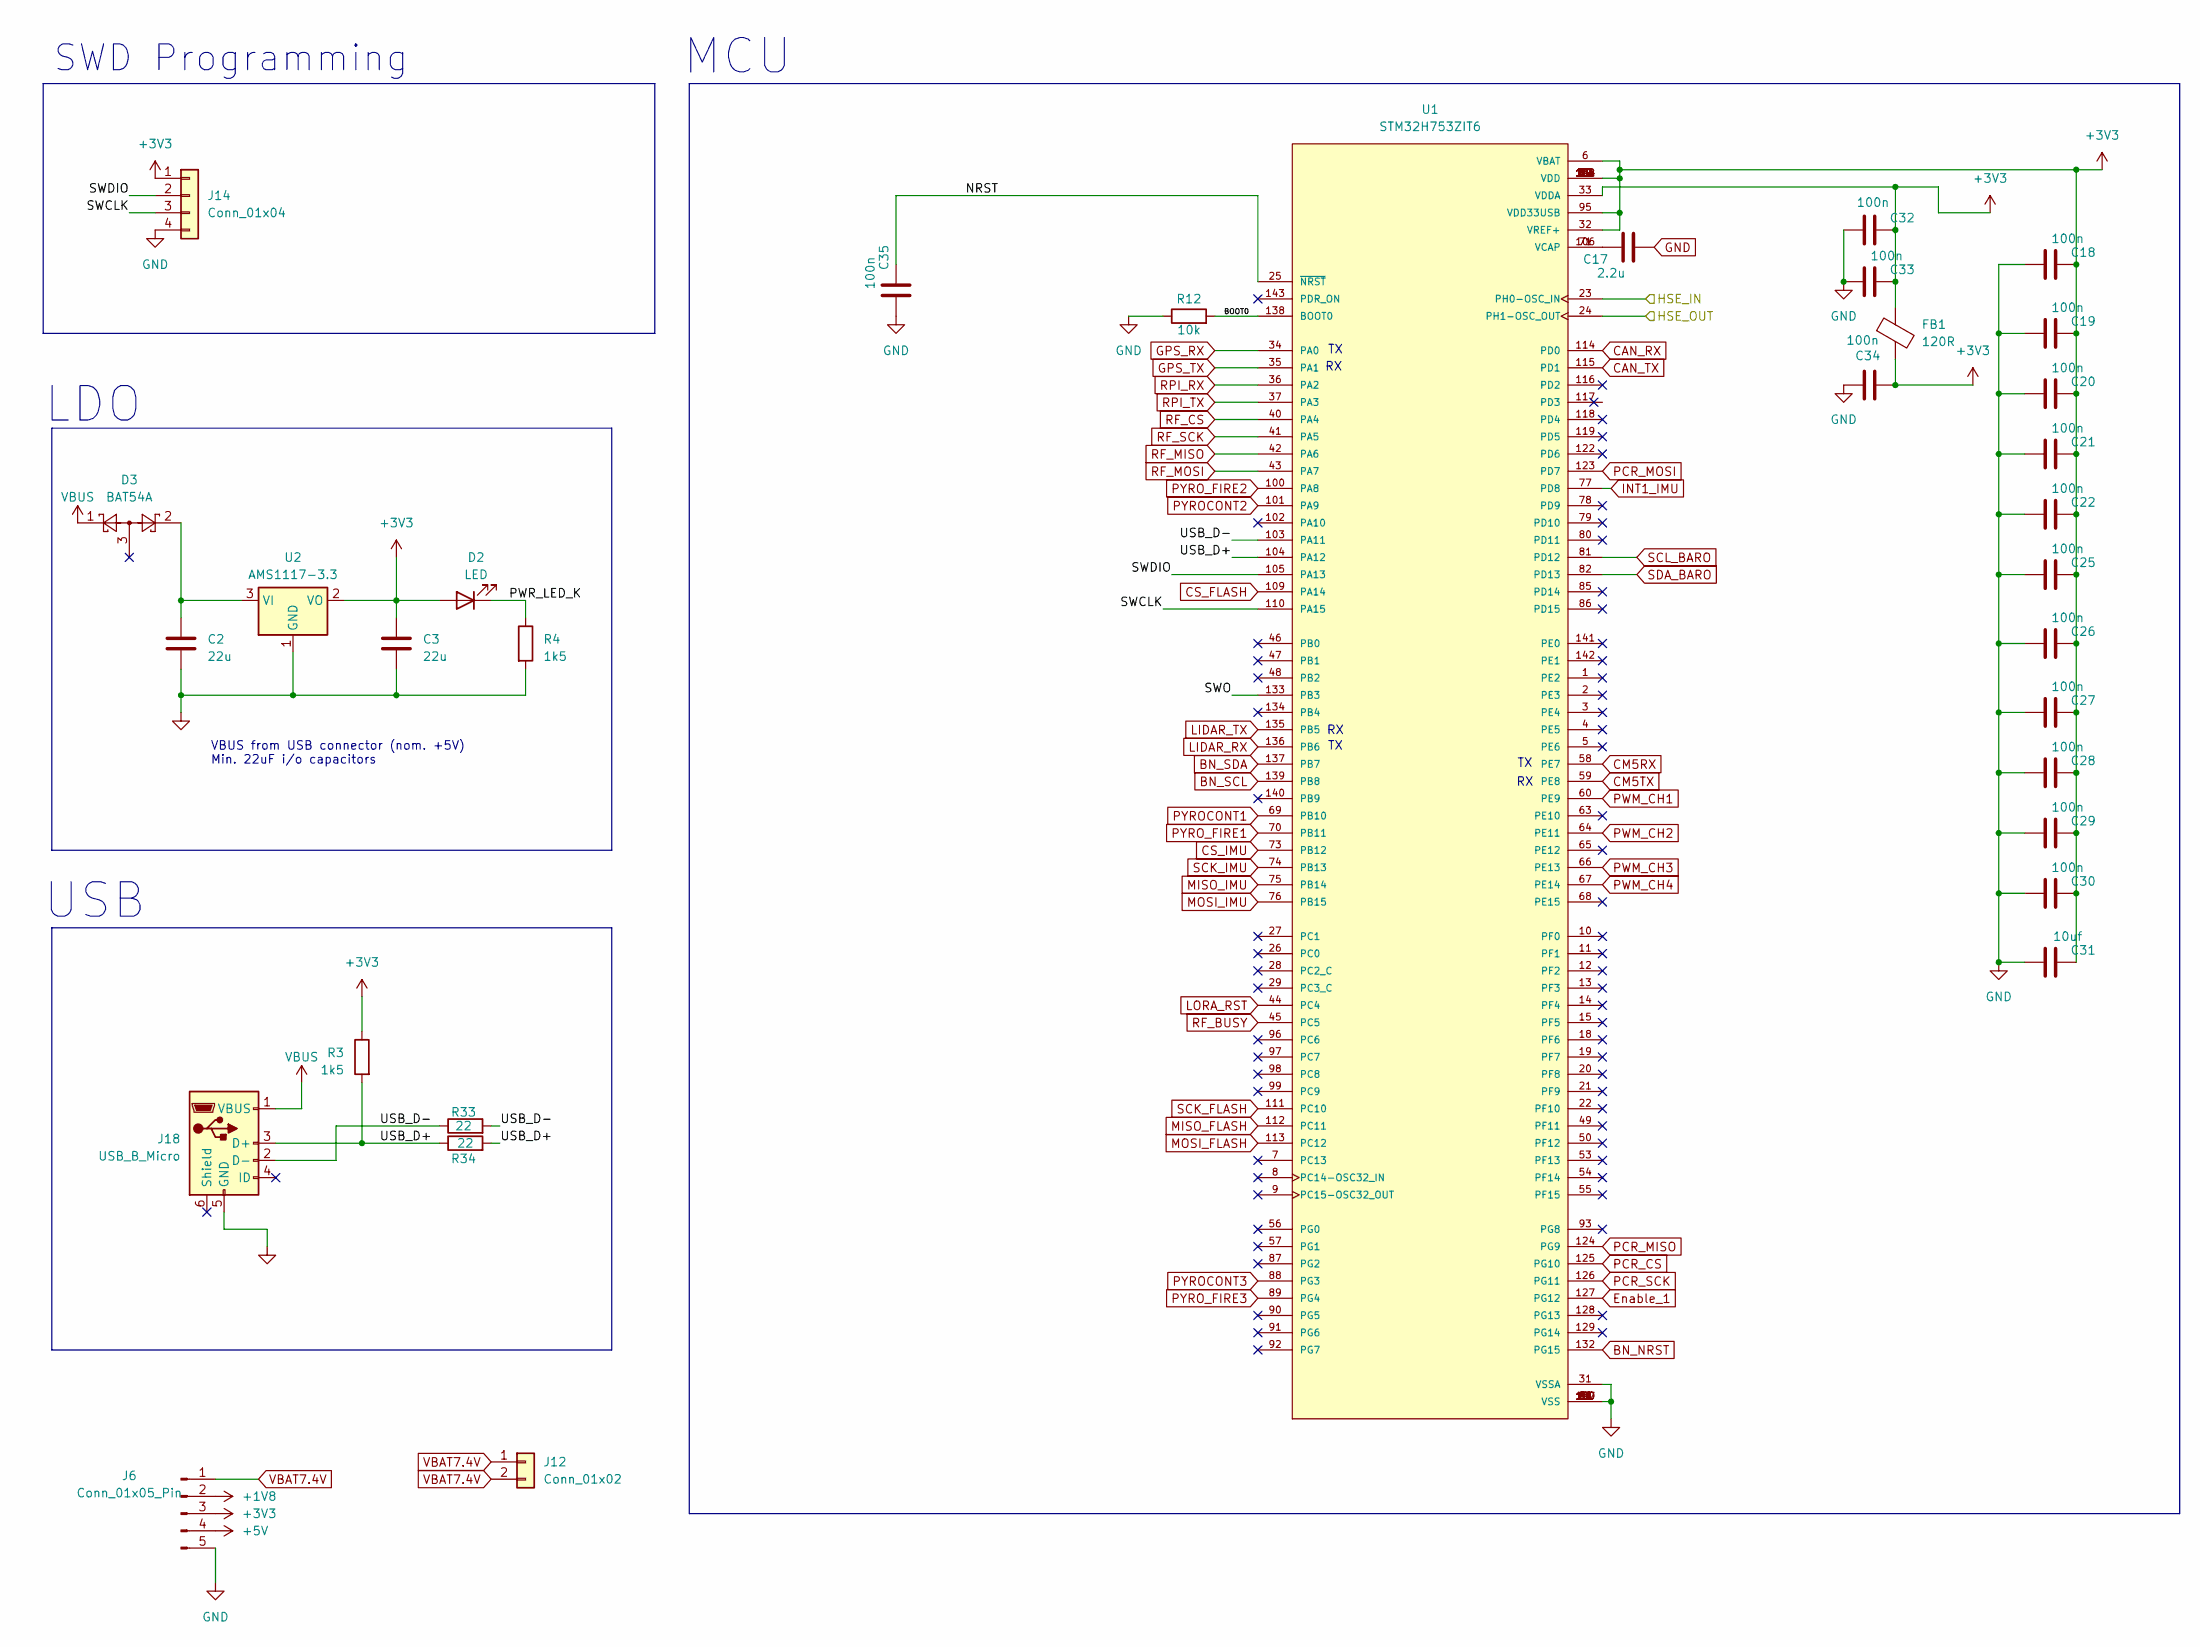
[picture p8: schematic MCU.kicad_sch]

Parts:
C2, C3: 22u; C_0805_2012Metric
C17: 2.2u; C_0402_1005Metric
C18, C19, C20, C21, C22, C25, C26, C27, C28, C29, C30, C32, C33, C34, C35: 100n; C_0402_1005Metric
C31: 10uf; C_0402_1005Metric
D2: LED; LED_0402_1005Metric
D3: BAT54A; SOT-23
FB1: 120R; IND_GZ1608_SNL
J6: Conn_01x05_Pin; JST_XH_B5B-XH-A_1x05_P2.50mm_Vertical
J12: Conn_01x02; JST_XH_S2B-XH-A_1x02_P2.50mm_Horizontal
J14: Conn_01x04; PinHeader_1x04_P2.54mm_Vertical
J18: USB_B_Micro; USB_Micro-B_Wuerth_629105150521
R3, R4: 1k5; R_0402_1005Metric
R12: 10k; R_0402_1005Metric
R33, R34: 22; R_0402_1005Metric
U1: STM32H753ZIT6; QFP50P2200X2200X160-144N; PARTREV 7
U2: AMS1117-3.3; SOT-223-3_TabPin2

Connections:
+1V8: J6.2; also elsewhere on the board
+3V3: C3.1, C18.1, C19.1, C20.1, C21.1, C22.1, C25.1, C26.1, C27.1, C28.1, C29.1, C30.1, C31.1, C32.1, C33.1, C34.1, D2.2 (A), FB1.1, FB1.2, J6.3, J14.1, R3.1, U1.6 (VBAT), U1.17 (VDD), U1.30 (VDD), U1.32 (VREF+), U1.33 (VDDA), U1.39 (VDD), U1.52 (VDD), U1.62 (VDD), U1.72 (VDD), U1.84 (VDD), U1.95 (VDD33USB), U1.108 (VDD), U1.121 (VDD), U1.131 (VDD), U1.144 (VDD), U2.2 (VO); also elsewhere on the board
+5V: J6.4; also elsewhere on the board
/Clocks/HSE_IN: U1.23 (PH0-OSC_IN); also elsewhere on the board
/Clocks/HSE_OUT: U1.24 (PH1-OSC_OUT); also elsewhere on the board
/MCU/BOOT0: R12.2, U1.138 (BOOT0)
/MCU/NRST: C35.1, U1.25 (~NRST)
/MCU/PWR_LED_K: D2.1 (K), R4.1
/MCU/SWCLK: J14.3, U1.110 (PA15)
/MCU/SWDIO: J14.2, U1.105 (PA13)
/MCU/SWO: U1.133 (PB3)
/MCU/USB_D+: J18.3 (D+), R3.2, R34.1, R34.2, U1.104 (PA12)
/MCU/USB_D-: J18.2 (D-), R33.1, R33.2, U1.103 (PA11)
BN_NRST: U1.132 (PG15); also elsewhere on the board
BN_SCL: U1.139 (PB8); also elsewhere on the board
BN_SDA: U1.137 (PB7); also elsewhere on the board
CAN_RX: U1.114 (PD0); also elsewhere on the board
CAN_TX: U1.115 (PD1); also elsewhere on the board
CM5RX: U1.58 (PE7); also elsewhere on the board
CM5TX: U1.59 (PE8); also elsewhere on the board
CS_FLASH: U1.109 (PA14); also elsewhere on the board
CS_IMU: U1.73 (PB12); also elsewhere on the board
Enable_1: U1.127 (PG12); also elsewhere on the board
GND: C2.2, C3.2, C17.2, C18.2, C19.2, C20.2, C21.2, C22.2, C25.2, C26.2, C27.2, C28.2, C29.2, C30.2, C31.2, C32.2, C33.2, C34.2, C35.2, J6.5, J14.4, J18.5 (GND), R4.2, R12.1, U1.16 (VSS), U1.31 (VSSA), U1.38 (VSS), U1.51 (VSS), U1.61 (VSS), U1.83 (VSS), U1.94 (VSS), U1.107 (VSS), U1.120 (VSS), U1.130 (VSS), U2.1 (GND); also elsewhere on the board
GPS_RX: U1.34 (PA0); also elsewhere on the board
GPS_TX: U1.35 (PA1); also elsewhere on the board
INT1_IMU: U1.77 (PD8); also elsewhere on the board
LIDAR_RX: U1.136 (PB6); also elsewhere on the board
LIDAR_TX: U1.135 (PB5); also elsewhere on the board
LORA_RST: U1.44 (PC4); also elsewhere on the board
MISO_FLASH: U1.112 (PC11); also elsewhere on the board
MISO_IMU: U1.75 (PB14); also elsewhere on the board
MOSI_FLASH: U1.113 (PC12); also elsewhere on the board
MOSI_IMU: U1.76 (PB15); also elsewhere on the board
unnamed: C17.1, U1.71 (VCAP), U1.106 (VCAP)
unnamed: C2.1, D3.2, U2.3 (VI)
PCR_CS: U1.125 (PG10); also elsewhere on the board
PCR_MISO: U1.124 (PG9); also elsewhere on the board
PCR_MOSI: U1.123 (PD7); also elsewhere on the board
PCR_SCK: U1.126 (PG11); also elsewhere on the board
PWM_CH1: U1.60 (PE9); also elsewhere on the board
PWM_CH2: U1.64 (PE11); also elsewhere on the board
PWM_CH3: U1.66 (PE13); also elsewhere on the board
PWM_CH4: U1.67 (PE14); also elsewhere on the board
PYROCONT1: U1.69 (PB10); also elsewhere on the board
PYROCONT2: U1.101 (PA9); also elsewhere on the board
PYROCONT3: U1.88 (PG3); also elsewhere on the board
PYRO_FIRE1: U1.70 (PB11); also elsewhere on the board
PYRO_FIRE2: U1.100 (PA8); also elsewhere on the board
PYRO_FIRE3: U1.89 (PG4); also elsewhere on the board
RF_BUSY: U1.45 (PC5); also elsewhere on the board
RF_CS: U1.40 (PA4); also elsewhere on the board
RF_MISO: U1.42 (PA6); also elsewhere on the board
RF_MOSI: U1.43 (PA7); also elsewhere on the board
RF_SCK: U1.41 (PA5); also elsewhere on the board
RPI_RX: U1.36 (PA2); also elsewhere on the board
RPI_TX: U1.37 (PA3); also elsewhere on the board
SCK_FLASH: U1.111 (PC10); also elsewhere on the board
SCK_IMU: U1.74 (PB13); also elsewhere on the board
SCL_BARO: U1.81 (PD12); also elsewhere on the board
SDA_BARO: U1.82 (PD13); also elsewhere on the board
VBAT7.4V: J6.1, J12.1, J12.2; also elsewhere on the board
VBUS: D3.1, J18.1 (VBUS)

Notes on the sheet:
SWD Programming
USB
VBUS from USB connector (nom. +5V) Min. 22uF i/o capacitors
LDO
MCU

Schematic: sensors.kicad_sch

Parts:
C36: 100n; C_0603_1608Metric
C39, C41, C42, C58: 100n; C_0402_1005Metric
C40: 2.2u; C_0402_1005Metric
C59: 10n; C_0402_1005Metric
J2: Conn_01x02_Pin; JST_XH_B2B-XH-A_1x02_P2.50mm_Vertical
J7: 532610471; MOLEX_532610471; PARTREV J; DigiKey_Part_Number WM7622CT-ND
R14, R17, R21, R22: 4.7k; R_0603_1608Metric
R32: 100Ω; R_0402_1005Metric
U3: BNO085; IC_BNO085; PARTREV v1.17
U4: ICM-42688-P; PQFN50P300X250X97-14N; PARTREV 1.2
U5: MS5611-01BA; LGA-8_3x5mm_P1.25mm

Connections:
+3V3: C36.1, C39.2, C40.2, C41.2, C42.2, C59.2, R14.1, R17.1, R21.1, R22.2, U3.3 (VDD), U3.28 (VDDIO), U4.5 (VDDIO), U4.8 (VDD), U5.1 (VDD), U5.2 (PS); also elsewhere on the board
+5V: J7.1; also elsewhere on the board
/Clocks/XINIMU: U3.27 (XIN32); also elsewhere on the board
/Clocks/XOUTIMU: U3.26 (XOUT32/CLKSEL1); also elsewhere on the board
BN_NRST: U3.11 (~RST); also elsewhere on the board
BN_SCL: R21.2, U3.19 (H_SCL/SCK/RX); also elsewhere on the board
BN_SDA: R22.1, U3.20 (H_SDA/H_MISO/TX); also elsewhere on the board
CAN_RX: J2.1; also elsewhere on the board
CAN_TX: J2.2; also elsewhere on the board
CS_IMU: U4.12 (AP_CS); also elsewhere on the board
GND: C36.2, C39.1, C40.1, C41.1, C42.1, C58.2, C59.1, J7.2, J7.S1 (SHIELD1), J7.S2 (SHIELD2), U3.2 (GND), U3.10 (CLKSEL0), U3.17 (SA0/H_MOSI), U3.25 (GNDIO), U4.6 (GND), U4.7 (RESV_7), U4.11 (RESV_11), U5.3 (GND), U5.4 (CSB), U5.5 (CSB); also elsewhere on the board
INT1_IMU: R32.2; also elsewhere on the board
LIDAR_RX: J7.4; also elsewhere on the board
LIDAR_TX: J7.3; also elsewhere on the board
MISO_IMU: U4.1 (AP_SDO/AP_AD0); also elsewhere on the board
MOSI_IMU: U4.14 (AP_SDA/AP_SDIO/AP_SDI); also elsewhere on the board
unnamed: C58.1, U3.9 (CAP)
unnamed: R32.1, U4.4 (INT1/INT)
SCK_IMU: U4.13 (AP_SCL/AP_SCLK); also elsewhere on the board
SCL_BARO: R17.2, U5.8 (SCLK); also elsewhere on the board
SDA_BARO: R14.2, U5.7 (SDI/SDA); also elsewhere on the board

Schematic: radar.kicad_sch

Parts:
C49, C66, C67: 100n; C_0402_1005Metric
C53: 10u; C_0402_1005Metric
IC7: A121-001-T&R; A121001TR; Mouser Part Number 925-A121-001-T&R
R15: 10k; R_0402_1005Metric
U7: TXS0108EPW; TSSOP-20_4.4x6.5mm_P0.65mm

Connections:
+1V8: C49.2, C53.2, C67.2, IC7.C2 (VRX_1), IC7.C9 (VTX_1), IC7.D1 (VRX_2), IC7.D10 (VTX_2), IC7.J1 (RESET_N), IC7.J9 (VDIG), IC7.K9 (VIO), U7.2 (VCCA); also elsewhere on the board
+3V3: C66.1, R15.1, U7.10 (OE), U7.19 (VCCB); also elsewhere on the board
/Clocks/XIN1: IC7.J10 (XIN); also elsewhere on the board
/Clocks/XOUT1: IC7.H10 (XOUT); also elsewhere on the board
/mmWave/1.8VCS: IC7.J2 (SPI_SS), U7.1 (A1)
/mmWave/1.8VMISO: IC7.K3 (SPI_MISO), U7.4 (A3)
/mmWave/1.8VMOSI: IC7.K6 (SPI_MOSI), U7.5 (A4)
/mmWave/1.8VSCK: IC7.K2 (SPI_CLK), U7.3 (A2)
Acc1: IC7.F10 (ENABLE), U7.6 (A5)
Enable_1: U7.15 (B5); also elsewhere on the board
GND: C49.1, C53.1, C66.2, C67.1, IC7.A3 (GND_1), IC7.A4 (GND_2), IC7.A5 (GND_3), IC7.A6 (GND_4), IC7.A7 (GND_5), IC7.A8 (GND_6), IC7.A9 (CTRL), IC7.B2 (GND_7), IC7.B9 (GND_8), IC7.B10 (GPIO3), IC7.C1 (GND_9), IC7.C10 (GND_10), IC7.D2 (GND_11), IC7.D9 (GND_12), IC7.E1 (GND_13), IC7.E2 (GND_14), IC7.E9 (GND_15), IC7.E10 (PLL_RF_TEST), IC7.F1 (GPIO1), IC7.F2 (GND_16), IC7.F9 (GND_17), IC7.G1 (GND_18), IC7.G10 (GND_19), IC7.H1 (GPIO2), IC7.H2 (GND_20), IC7.H9 (GND_21), IC7.J3 (GND_22), IC7.J5 (GND_23), IC7.J6 (GND_24), IC7.J8 (GND_25), IC7.K4 (GND_26), IC7.K5 (GPIO4), IC7.K7 (GND_27), U7.11 (GND); also elsewhere on the board
PCR_CS: R15.2, U7.17 (B3); also elsewhere on the board
PCR_MISO: U7.18 (B2); also elsewhere on the board
PCR_MOSI: U7.20 (B1); also elsewhere on the board
PCR_SCK: U7.16 (B4); also elsewhere on the board

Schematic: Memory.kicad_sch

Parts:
C1: 10uF; C_0402_1005Metric
IC1: W25Q128JVFIQ; SOIC127P1032X264-16N; Mouser Part Number 454-W25Q128JVFIQ
R11: 10k; R_0402_1005Metric

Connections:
+3V3: C1.2, IC1.1 (IO3), IC1.2 (VCC), IC1.9 (IO2), R11.1; also elsewhere on the board
CS_FLASH: IC1.7 (~CS), R11.2; also elsewhere on the board
GND: C1.1, IC1.10 (GND); also elsewhere on the board
MISO_FLASH: IC1.8 (DO_(IO1)); also elsewhere on the board
MOSI_FLASH: IC1.15 (DI_(IO0)); also elsewhere on the board
SCK_FLASH: IC1.16 (CLK); also elsewhere on the board

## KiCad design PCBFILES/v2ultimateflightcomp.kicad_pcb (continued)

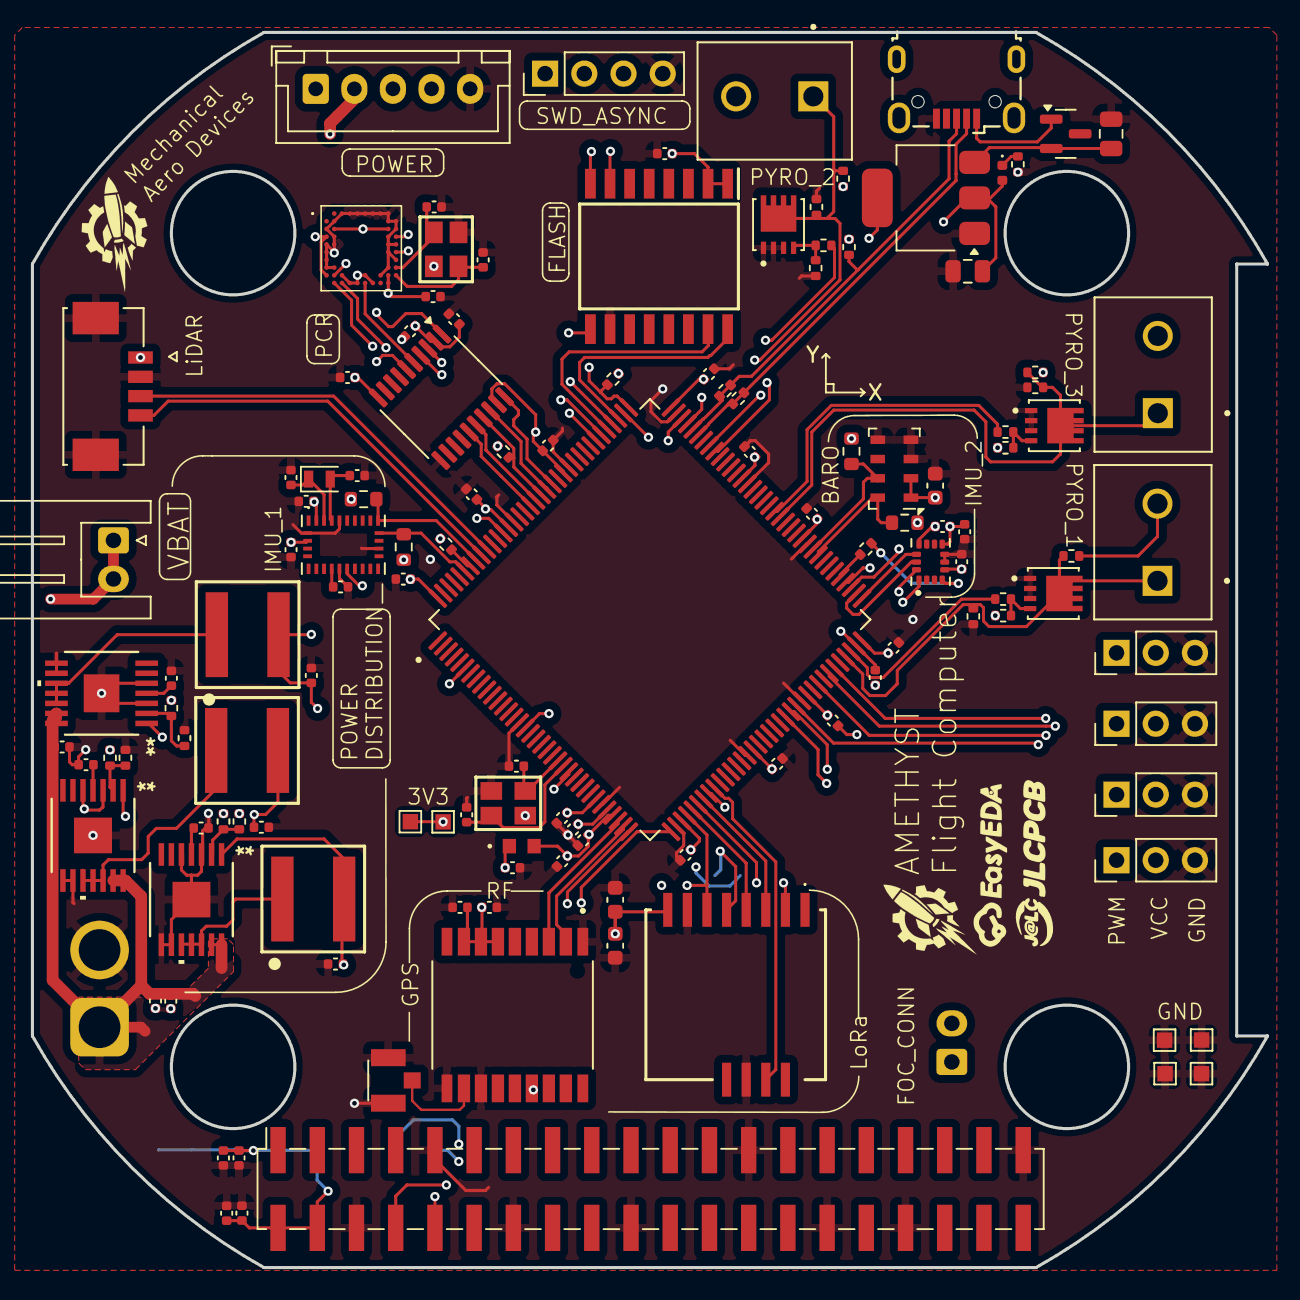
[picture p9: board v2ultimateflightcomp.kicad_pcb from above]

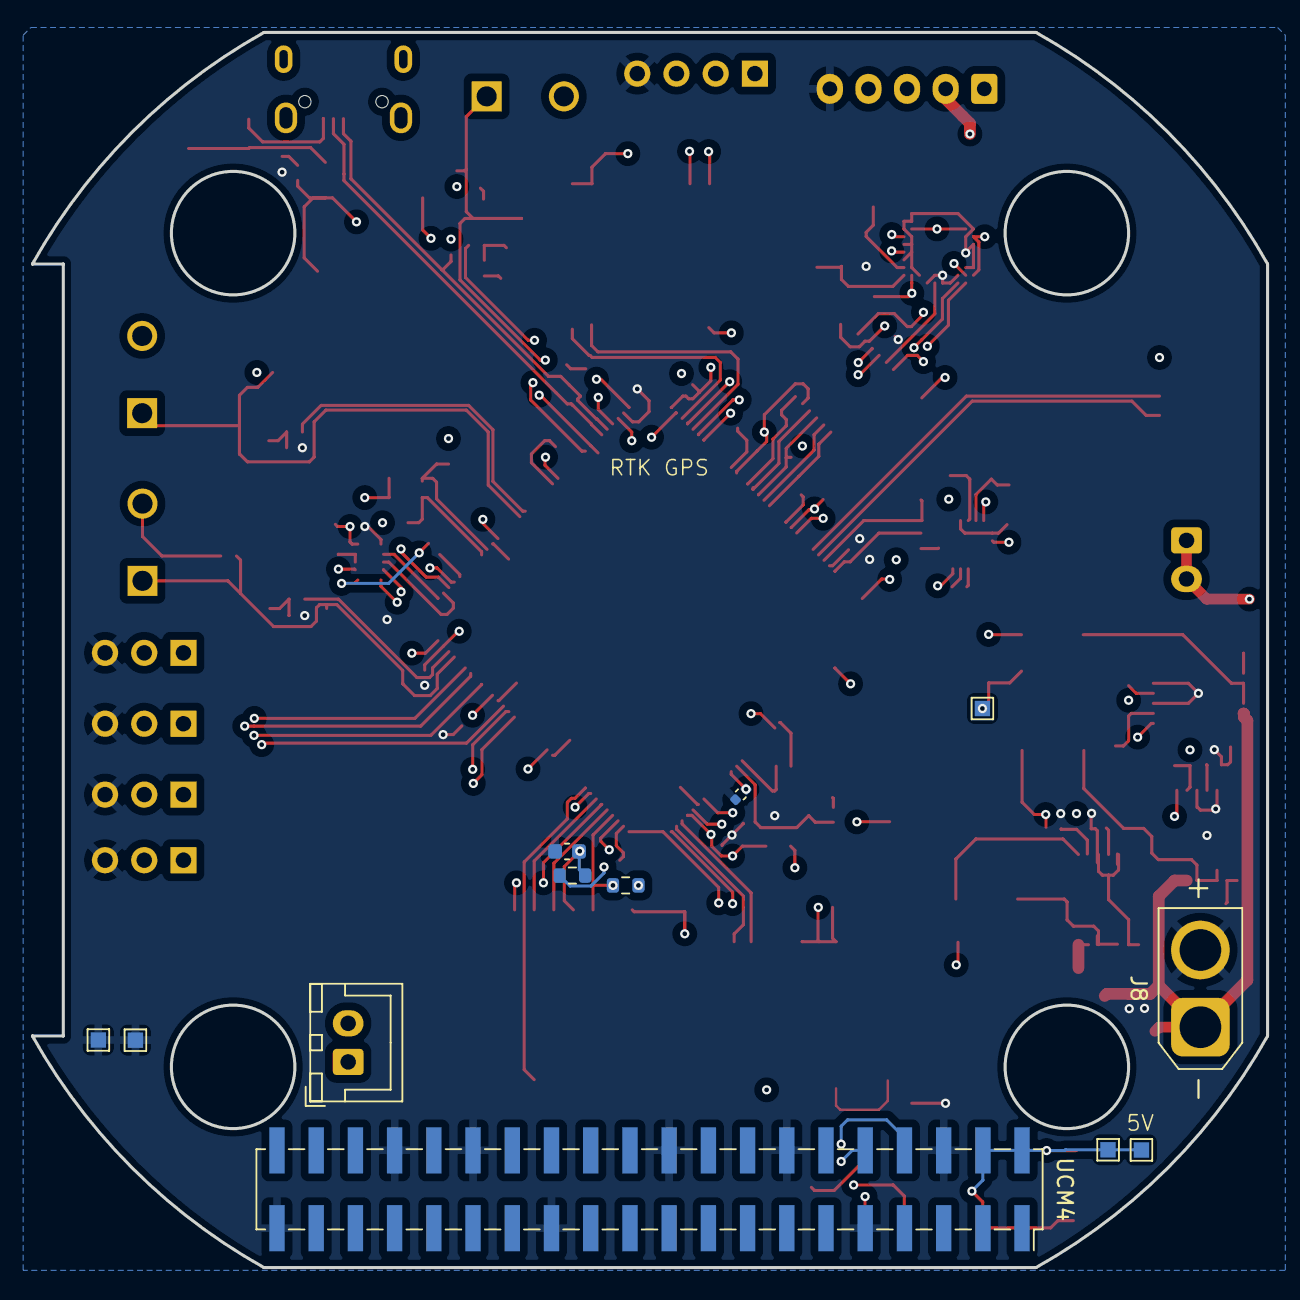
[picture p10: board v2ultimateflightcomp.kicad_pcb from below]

Board: 6 copper layers, 80.0 x 80.0 mm, 140 parts (12 on the bottom side), 86 nets.

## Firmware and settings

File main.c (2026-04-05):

#include "flight_computer.h"

#include <stdbool.h>
#include <stddef.h>
#include <stdint.h>

/*
 * Replace these mock transports with your actual STM32 HAL bindings.
 * They exist so the project has a complete entry point and host-side syntax checks.
 */

static fc_status_t mock_i2c_write(void *context, uint8_t address, const uint8_t *tx, size_t tx_len)
{
    (void)context;
    (void)address;
    (void)tx;
    (void)tx_len;
    return FC_STATUS_OK;
}

static fc_status_t mock_i2c_read(void *context, uint8_t address, uint8_t *rx, size_t rx_len)
{
    size_t index;
    (void)context;
    (void)address;

    for (index = 0u; index < rx_len; ++index)
    {
        rx[index] = 0u;
    }
    return FC_STATUS_OK;
}

static fc_status_t mock_i2c_write_read(void *context,
                                       uint8_t address,
                                       const uint8_t *tx,
                                       size_t tx_len,
                                       uint8_t *rx,
                                       size_t rx_len)
{
    (void)tx;
    (void)tx_len;
    return mock_i2c_read(context, address, rx, rx_len);
}

static void mock_delay_ms(void *context, uint32_t delay_ms)
{
    (void)context;
    (void)delay_ms;
}

static fc_status_t mock_spi_select(void *context, bool selected)
{
    (void)context;
    (void)selected;
    return FC_STATUS_OK;
}

static fc_status_t mock_spi_transfer(void *context, const uint8_t *tx, uint8_t *rx, size_t len)
{
    size_t index;
    (void)context;
    (void)tx;

    if (rx != NULL)
    {
        for (index = 0u; index < len; ++index)
        {
            rx[index] = 0u;
        }
    }
    return FC_STATUS_OK;
}

static fc_status_t mock_uart_write(void *context, const uint8_t *tx, size_t len)
{
    (void)context;
    (void)tx;
    (void)len;
    return FC_STATUS_OK;
}

static fc_status_t mock_uart_read(void *context,
                                  uint8_t *rx,
                                  size_t len,
                                  uint32_t timeout_ms,
                                  size_t *received_len)
{
    size_t index;
    (void)context;
    (void)timeout_ms;

    for (index = 0u; index < len; ++index)
    {
        rx[index] = 0u;
    }

    if (received_len != NULL)
    {
        *received_len = 0u;
    }
    return FC_STATUS_OK;
}

static fc_status_t mock_can_send(void *context, const fc_can_frame_t *frame)
{
    (void)context;
    (void)frame;
    return FC_STATUS_OK;
}

static fc_status_t mock_pwm_set(void *context, uint8_t channel, float duty_0_to_1)
{
    (void)context;
    (void)channel;
    (void)duty_0_to_1;
    return FC_STATUS_OK;
}

static uint32_t mock_millis(void *context)
{
    static uint32_t time_ms = 0u;
    (void)context;
    time_ms += 10u;
    return time_ms;
}

static fc_status_t mock_pyro_set_armed(void *context, bool armed)
{
    (void)context;
    (void)armed;
    return FC_STATUS_OK;
}

static bool mock_pyro_continuity_ok(void *context)
{
    (void)context;
    return true;
}

static fc_status_t mock_pyro_fire_channel(void *context, uint8_t channel)
{
    (void)context;
    (void)channel;
    return FC_STATUS_OK;
}

int main(void)
{
    fc_i2c_bus_t i2c_bus = {0};
    fc_spi_bus_t spi_bus = {0};
    fc_uart_bus_t uart_bus = {0};
    fc_can_bus_t can_bus = {0};
    fc_pwm_bus_t pwm_bus = {0};
    fc_time_source_t time_source = {0};
    fc_pyro_interface_t pyro = {0};
    fc_board_config_t board = {0};
    fc_flight_computer_t computer = {0};

    i2c_bus.write = mock_i2c_write;
    i2c_bus.read = mock_i2c_read;
    i2c_bus.write_read = mock_i2c_write_read;
    i2c_bus.delay_ms = mock_delay_ms;

    spi_bus.select = mock_spi_select;
    spi_bus.transfer = mock_spi_transfer;
    spi_bus.delay_ms = mock_delay_ms;

    uart_bus.write = mock_uart_write;
    uart_bus.read = mock_uart_read;

    can_bus.send = mock_can_send;
    pwm_bus.set_normalized = mock_pwm_set;
    time_source.millis = mock_millis;
    pyro.set_armed = mock_pyro_set_armed;
    pyro.continuity_ok = mock_pyro_continuity_ok;
    pyro.fire_channel = mock_pyro_fire_channel;

    board.baro_i2c = &i2c_bus;
    board.imu1_i2c = &i2c_bus;
    board.imu2_spi = &spi_bus;
    board.lidar_uart = &uart_bus;
    board.fdcan = &can_bus;
    board.gps_uart = &uart_bus;
    board.rpi_uart = &uart_bus;
    board.cm5_uart = &uart_bus;
    board.fin_uart = &uart_bus;
    board.pwm = &pwm_bus;
    board.lora_spi = &spi_bus;
    board.flash_spi = &spi_bus;
    board.mmwave_spi = &spi_bus;
    board.pyro = &pyro;
    board.time = &time_source;

    if (FlightComputer_Init(&computer, &board) == FC_STATUS_OK)
    {
        (void)FlightComputer_Step(&computer);
    }

    return 0;
}

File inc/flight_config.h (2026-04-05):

#ifndef FLIGHT_CONFIG_H
#define FLIGHT_CONFIG_H

#define FC_ONE_G_MPS2 9.80665f

#define FC_MS5611_I2C_ADDRESS 0x77u
#define FC_BNO085_I2C_ADDRESS 0x4Au

#define FC_ZED_F9P_RATE_HZ 15u

#define FC_LAUNCH_ACCEL_THRESHOLD_G 1.2f
#define FC_BURNOUT_ACCEL_THRESHOLD_G 0.5f
#define FC_DESCENT_ACCEL_THRESHOLD_G 1.0f

#define FC_BURNOUT_CONFIRM_MS 120u
#define FC_APOGEE_MIN_ALTITUDE_M 30.0f
#define FC_CM5_LINK_TIMEOUT_MS 250u

#define FC_MAX_LANDING_CROSSRANGE_M 50.0f
#define FC_MIN_RTK_SATELLITES 12u

#define FC_SUICIDE_BURN_ALTITUDE_OFFSET_M 1.0f
#define FC_SUICIDE_BURN_SAFETY_MARGIN_M 4.0f
#define FC_SECOND_STAGE_MAX_DECEL_MPS2 35.0f
#define FC_IGNITION_LATENCY_S 0.20f

#define FC_FLASH_LOG_SECTOR_SIZE 4096u
#define FC_FLASH_LOG_PAGE_SIZE 256u

#define FC_DEFAULT_WAYPOINT_X_M 0.0f
#define FC_DEFAULT_WAYPOINT_Y_M 0.0f

#endif

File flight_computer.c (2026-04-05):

#include "flight_computer.h"

#include <math.h>
#include <stdio.h>
#include <string.h>

#define CM5_SYNC_1 0xA5u
#define CM5_SYNC_2 0x5Au
#define CM5_MSG_STATE 0x01u
#define CM5_MSG_ASCENT_MODE 0x10u
#define CM5_MSG_PRO_NAV_MODE 0x11u
#define CM5_MSG_NMPC_MODE 0x12u
#define CM5_MSG_FIN_RESPONSE 0x81u

static uint32_t fc_now_ms(const fc_flight_computer_t *computer)
{
    if (computer != NULL && computer->board.time != NULL && computer->board.time->millis != NULL)
    {
        return computer->board.time->millis(computer->board.time->context);
    }

    return (computer != NULL) ? (computer->ukf_state.timestamp_ms + 10u) : 0u;
}

static float fc_clampf(float value, float min_value, float max_value)
{
    if (value < min_value)
    {
        return min_value;
    }
    if (value > max_value)
    {
        return max_value;
    }
    return value;
}

static fc_vec3_t fc_vec3_add(fc_vec3_t a, fc_vec3_t b)
{
    fc_vec3_t result = {a.x + b.x, a.y + b.y, a.z + b.z};
    return result;
}

static fc_vec3_t fc_vec3_scale(fc_vec3_t a, float scale)
{
    fc_vec3_t result = {a.x * scale, a.y * scale, a.z * scale};
    return result;
}

static float fc_vec3_length_xy(fc_vec3_t a)
{
    return sqrtf((a.x * a.x) + (a.y * a.y));
}

static fc_quat_t fc_quat_normalize(fc_quat_t q)
{
    float norm = sqrtf((q.w * q.w) + (q.x * q.x) + (q.y * q.y) + (q.z * q.z));

    if (norm > 0.0001f)
    {
        q.w /= norm;
        q.x /= norm;
        q.y /= norm;
        q.z /= norm;
    }
    else
    {
        q.w = 1.0f;
        q.x = 0.0f;
        q.y = 0.0f;
        q.z = 0.0f;
    }

    return q;
}

static void fc_quat_to_euler(const fc_quat_t *q, float *roll_rad, float *pitch_rad, float *yaw_rad)
{
    const float sinr_cosp = 2.0f * ((q->w * q->x) + (q->y * q->z));
    const float cosr_cosp = 1.0f - (2.0f * ((q->x * q->x) + (q->y * q->y)));
    const float sinp = 2.0f * ((q->w * q->y) - (q->z * q->x));
    const float siny_cosp = 2.0f * ((q->w * q->z) + (q->x * q->y));
    const float cosy_cosp = 1.0f - (2.0f * ((q->y * q->y) + (q->z * q->z)));

    if (roll_rad != NULL)
    {
        *roll_rad = atan2f(sinr_cosp, cosr_cosp);
    }
    if (pitch_rad != NULL)
    {
        *pitch_rad = (fabsf(sinp) >= 1.0f) ? copysignf(1.57079632679f, sinp) : asinf(sinp);
    }
    if (yaw_rad != NULL)
    {
        *yaw_rad = atan2f(siny_cosp, cosy_cosp);
    }
}

static uint16_t fc_crc16_ccitt(const uint8_t *buffer, size_t len)
{
    uint16_t crc = 0xFFFFu;
    size_t index;
    uint8_t bit;

    for (index = 0u; index < len; ++index)
    {
        crc ^= (uint16_t)buffer[index] << 8;
        for (bit = 0u; bit < 8u; ++bit)
        {
            crc = (crc & 0x8000u) ? (uint16_t)((crc << 1) ^ 0x1021u) : (uint16_t)(crc << 1);
        }
    }

    return crc;
}

static fc_status_t fc_send_cm5_frame(fc_flight_computer_t *computer,
                                     uint8_t message_id,
                                     const uint8_t *payload,
                                     uint8_t payload_len)
{
    uint8_t frame[128] = {0};
    uint16_t crc;
    size_t total_len;

    if (computer == NULL || computer->board.cm5_uart == NULL || computer->board.cm5_uart->write == NULL)
    {
        return FC_STATUS_INVALID_ARG;
    }

    total_len = (size_t)payload_len + 6u;
    if (total_len > sizeof(frame))
    {
        return FC_STATUS_INVALID_ARG;
    }

    frame[0] = CM5_SYNC_1;
    frame[1] = CM5_SYNC_2;
    frame[2] = message_id;
    frame[3] = payload_len;
    if (payload_len > 0u && payload != NULL)
    {
        memcpy(&frame[4], payload, payload_len);
    }

    crc = fc_crc16_ccitt(&frame[2], (size_t)payload_len + 2u);
    frame[4u + payload_len] = (uint8_t)(crc & 0xFFu);
    frame[5u + payload_len] = (uint8_t)(crc >> 8);
    return computer->board.cm5_uart->write(computer->board.cm5_uart->context, frame, total_len);
}

static bool fc_parse_cm5_frame(const uint8_t *buffer,
                               size_t len,
                               uint8_t *message_id,
                               const uint8_t **payload,
                               uint8_t *payload_len)
{
    uint16_t received_crc;
    uint16_t computed_crc;
    uint8_t length;

    if (buffer == NULL || len < 6u)
    {
        return false;
    }

    if (buffer[0] != CM5_SYNC_1 || buffer[1] != CM5_SYNC_2)
    {
        return false;
    }

    length = buffer[3];
    if (len < (size_t)length + 6u)
    {
        return false;
    }

    received_crc = (uint16_t)(((uint16_t)buffer[5u + length] << 8) | buffer[4u + length]);
    computed_crc = fc_crc16_ccitt(&buffer[2], (size_t)length + 2u);
    if (received_crc != computed_crc)
    {
        return false;
    }

    *message_id = buffer[2];
    *payload_len = length;
    *payload = &buffer[4];
    return true;
}

static fc_status_t fc_send_fin_command_uart(fc_flight_computer_t *computer, const fc_fin_command_t *command)
{
    char packet[96];
    int len;

    if (computer == NULL || command == NULL || computer->board.fin_uart == NULL ||
        computer->board.fin_uart->write == NULL)
    {
        return FC_STATUS_UNSUPPORTED;
    }

    len = snprintf(packet,
                   sizeof(packet),
                   "$FIN,%.2f,%.2f,%.2f,%.2f\n",
                   command->fin1_deg,
                   command->fin2_deg,
                   command->fin3_deg,
                   command->fin4_deg);
    if (len <= 0)
    {
        return FC_STATUS_ERROR;
    }

    return computer->board.fin_uart->write(computer->board.fin_uart->context,
                                           (const uint8_t *)packet,
                                           (size_t)len);
}

static fc_status_t fc_update_navigation_suite(fc_flight_computer_t *computer, bool include_gps)
{
    float lidar_range_m = 0.0f;
    mmwave_measurement_t mmwave_measurement = {0};

    if (readBaroPressure(computer) == FC_STATUS_OK)
    {
        /* Baro is optional in a single step as long as the previous sample is still valid. */
    }
    (void)readOrientationRaw1(computer);
    (void)readOrientationRaw2(computer);

    if (computer->lidar.uart != NULL && lidar_uart_poll(&computer->lidar, &lidar_range_m) == FC_STATUS_OK)
    {
        computer->lidar_range_m = lidar_range_m;
    }

    if (computer->mmwave.initialized && mmwave_doppler_read(&computer->mmwave, &mmwave_measurement) ==
                                            FC_STATUS_OK && mmwave_measurement.valid)
    {
        computer->ukf_state.velocity_mps.z = -mmwave_measurement.radial_velocity_mps;
    }

    if (include_gps)
    {
        (void)ReadGPS(computer);
    }

    return UKFState(computer, fc_now_ms(computer));
}

static bool fc_detect_launch(const fc_flight_computer_t *computer)
{
    return computer != NULL && computer->ukf_state.acceleration_mps2.z >
                                   (FC_LAUNCH_ACCEL_THRESHOLD_G * FC_ONE_G_MPS2);
}
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
